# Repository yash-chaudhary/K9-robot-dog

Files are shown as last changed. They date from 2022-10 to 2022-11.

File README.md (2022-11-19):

# K9 Robot Dog

The COVID-19 pandemic gripped the world with its harsh lockdowns, lonely isolation, and imaginary
human contact. It turned loving families into raging chihuahua’s. But it was our pets that continued to
love us unconditionally. This report will demonstrate the development of K9 - man’s best robot friend

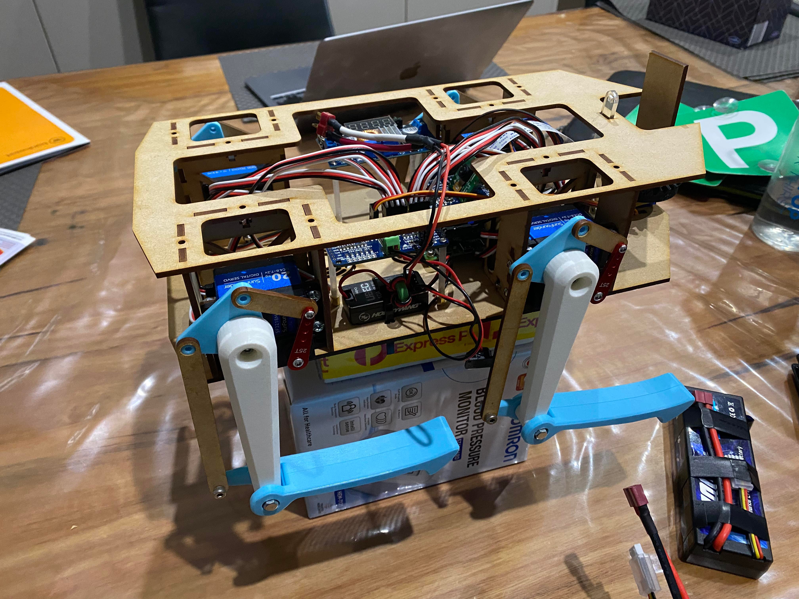
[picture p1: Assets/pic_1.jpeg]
Image of Physical Robot 1

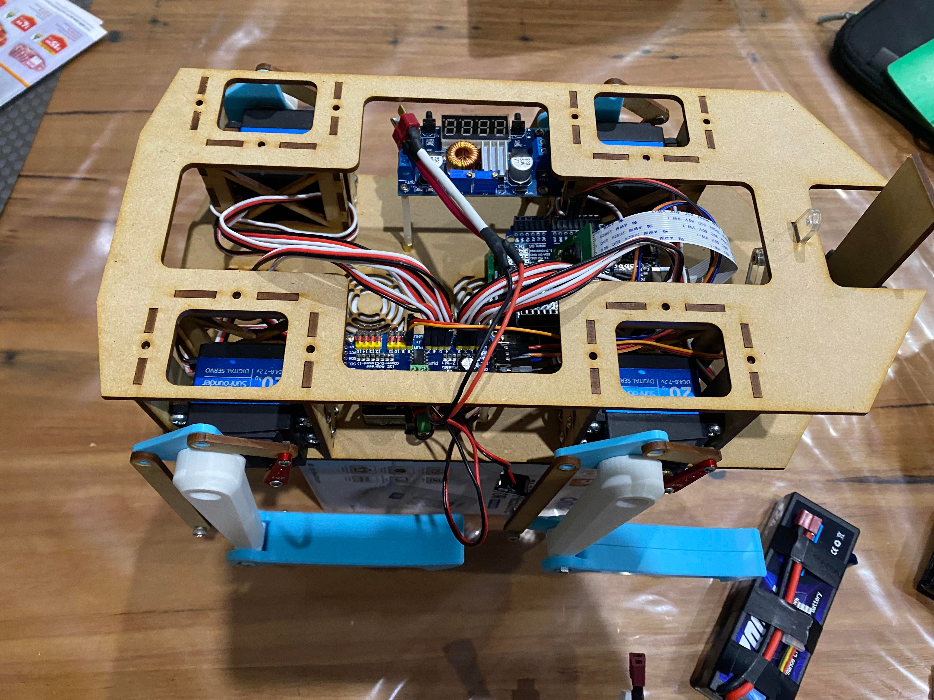
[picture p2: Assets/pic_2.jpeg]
Image of Physical Robot 2


### Software Design

Python was used to program a Raspberry Pi 4 Model B to leverage the open source real-time computer vision library, openCV. Using a
camera module, this python library is able to define the landmarks on a hand(s) to figure out how many figures a person is holding up
in real-time. Once it is able to recognise the gesture it sends this number as a command via the UART communication protocol to an
Arduino Uno which reads the command and executes the routine corresponding to the command. The Arduino Uno is a microcontroller as opposed
to a microprocesser which allows to it control it's I/O peripherals quite quickly which is incredibly important for the controlled motion
of quadrupedal motion.

As an aside, a couple of hours before the reveal of the robot, the gesture recogition software had an undetected bug. To restore
motion to the robot, an ultrasonic sensor was used, where instead of using a camera module with gesture recognition the ultrasonic sensor would detect the distance between itself and an obstacle in its field of view. Different distance thresholds away from the ultrasonic sensor were defined to control the movement of the robot with a 1 second delay between each command.

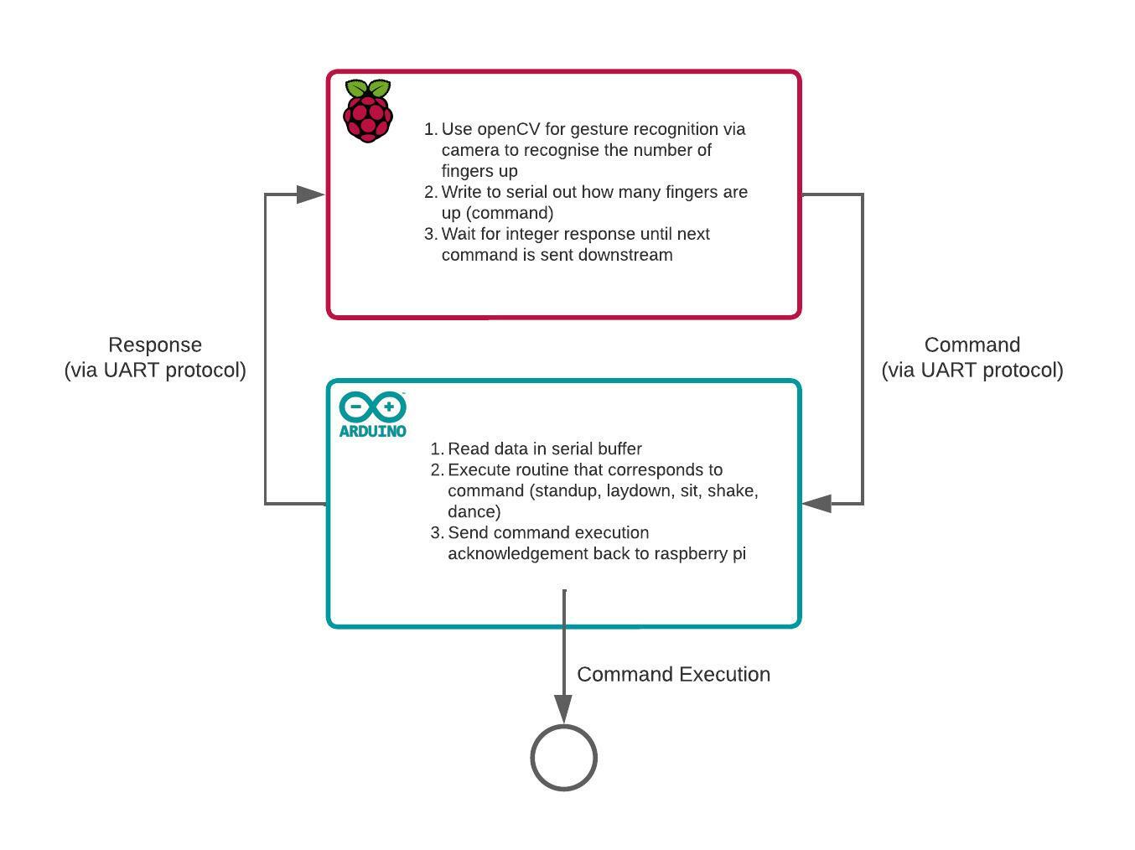
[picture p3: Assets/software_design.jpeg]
Image of Software Design


### Electrical Design

The first electronics track is the power transmission used to command the servo motors and it involves a 7.4V two-cell lithium polymer battery connected to a DPDT switch. The switch controls the power supply to a buck converter (DC-DC converter) that drops the 7.4V from the LiPo batteries to a 5V supply. The output from the buck converter is a regulated 5V supply from a USB-A connector that is connected to a Raspberry Pi Model 4 B via USB-C. The USB-A port from the Raspberry Pi is then connected to the serial port of the Arduino. Then using the 5V output pin on the Arduino, the PCA9685 Servo Driver is powered by connecting the 5V output to the PCA9685 VCC pin. This VCC pin is strictly used to power the PCA9685 chip. Other pins are required to ensure the servo driver works. The ground pin of the servo driver is connected to the ground pin on the Arduino and the SDA (serial data) and SCL (serial clock) are connected to the SDA and SCL pins on newer Arduinos or analogue pin 4 and 5 respectively on older Arduinos. These two pins allow the Arduino and PCA9685 to communicate to each other via the I2C communication protocol. This completes the power supply to the Raspberry Pi, Arduino and PCA9685 that are used to command the servo motors. The second electronics track is used to power the servo motors. Again a 7.4V two cell lithium polymer battery is used and it is connected to a universal battery eliminator circuit (essentially another buck converter) that steps down the battery supply voltage from 7.4V to 6V at a maximum supply current of 10A. The output of the universal battery eliminator circuit is connected to the terminal block on the PCA9685, and it also has a SPST switch to control the power supply. Each of the 3-pin servo motors that need to be controlled are connected to the PCA9685 where the top pin is the PWM signal pin, the middle pin is the V+ supply coming from the external battery power supply, and the last pin being ground. The completes the circuit to supply power to all the servos.

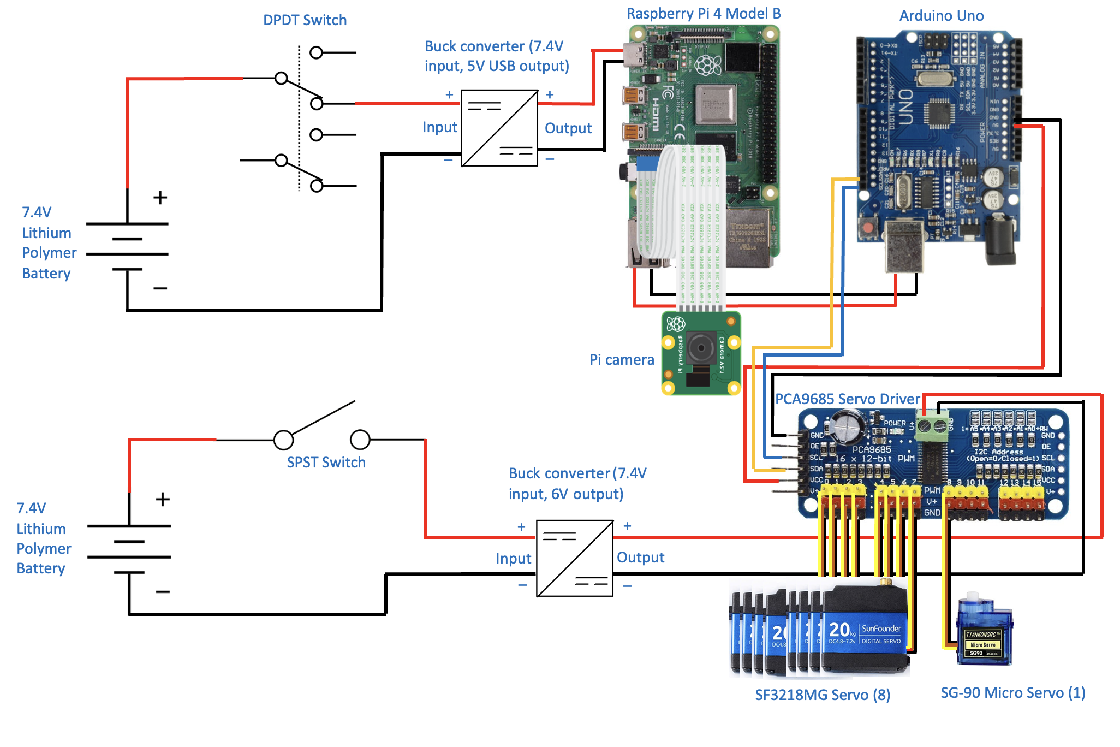
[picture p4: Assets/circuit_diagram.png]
Image of Electrical Design


### Mechanical Design

Calculations were conducted find out the max loading the servo motors would withstand. After this, the parts were designed in
Solidworks with load bearing components undergoing Finite Element Analysis (FEA) to ensure they don't fail under load. These components
were the ones that were going to be 3D printed. The rest of the components were laser cut with MDF and acrylic. One of the highlights
for the design was the use of captive nut and bolt t-solts that removed the need for any permanent joints in the design. Another insight was
that traditional robot dog designs have the mass of the servo motors controlling the lower leg was overhanging from the chassis, this design can lead to instabilities due to the potential for moments to occur which can topple the robot in the roll axis. So the goal was
to find a different design that kept the distribution of mass closer to the centre of mass to increase stability and handling of the robot during movements. A servo configuration that retained both the servos within the chassis with no large mass overhangs was found. The result is that stability was increased relative to other quadruped designs as the mass is concentrated closer to the centre of mass instead of hanging off the outer parts of the legs which can cause unwanted moments when moving the robot. Also the robot deliberating had a wider
body to further increase stability

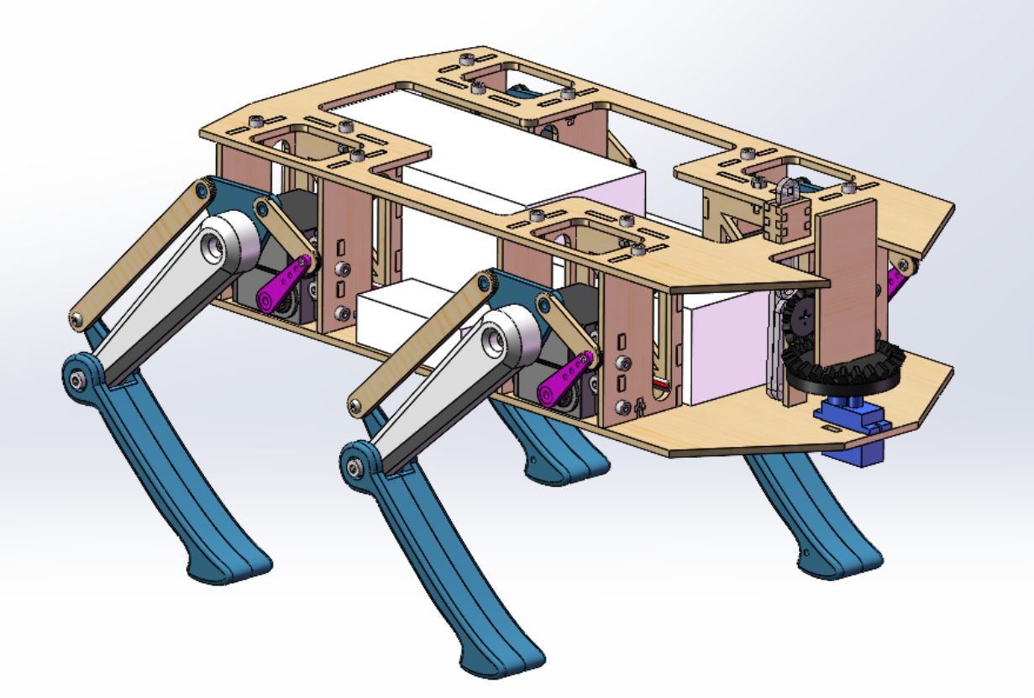
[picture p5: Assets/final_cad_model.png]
Image of CAD design

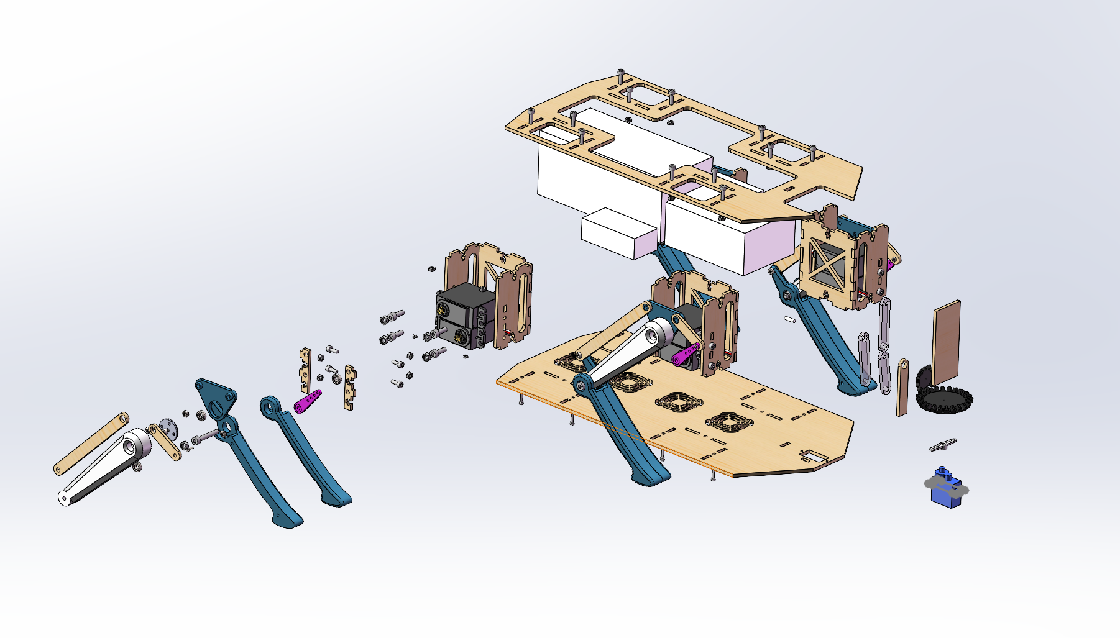
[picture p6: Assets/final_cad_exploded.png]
Image of CAD exploded view


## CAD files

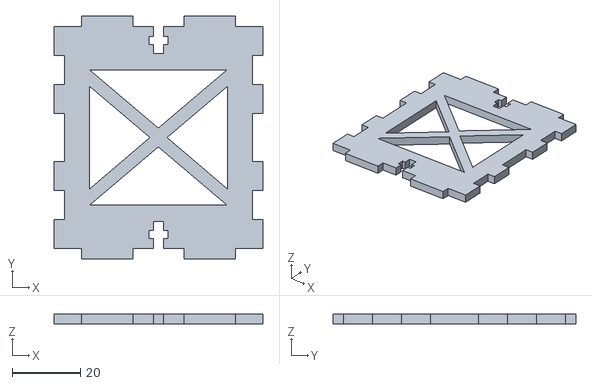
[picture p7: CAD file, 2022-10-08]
CAD/Chassis parts/Motor Back Plate (L 55mm W 65 mm D 3mm).stl
61.0 x 71.0 x 3.00

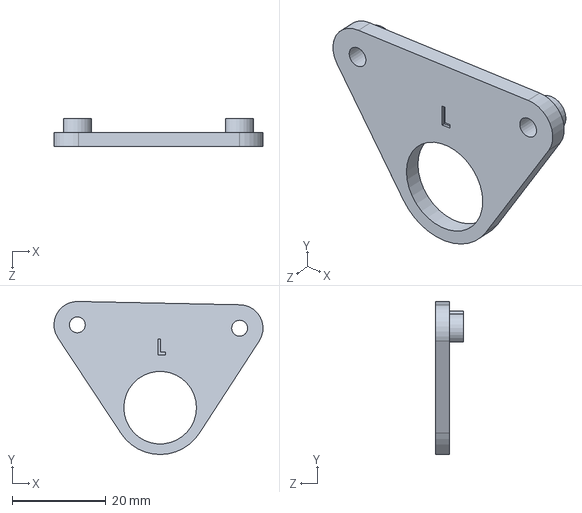
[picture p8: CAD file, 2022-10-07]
CAD/Leg parts/production_parts/15-5mm_left_linkage_plate.SLDPRT
44.6 x 32.7 x 6.00 mm

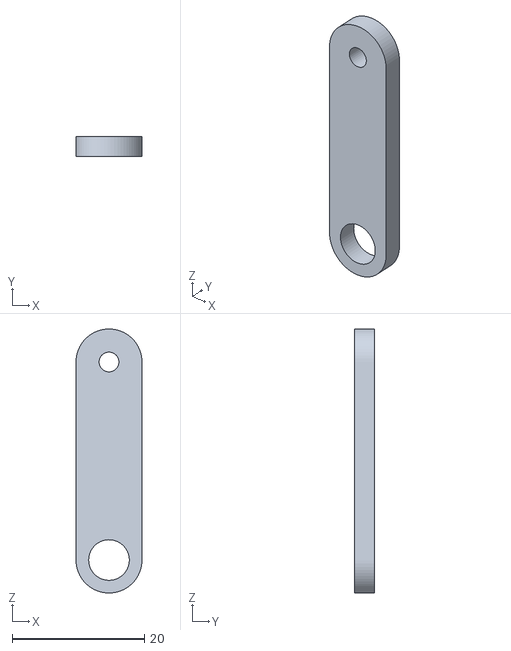
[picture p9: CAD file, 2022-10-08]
CAD/Leg parts/production_parts/linkages/V4_30mm_solid_arm v2.stl
10.0 x 3.00 x 40.0

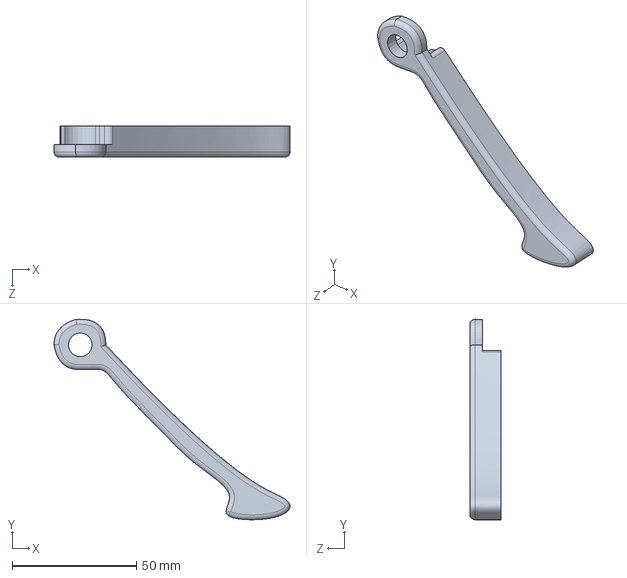
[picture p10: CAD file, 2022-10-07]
CAD/Leg parts/production_parts/lower_leg_v2/100mm_OUTER_RIGHT_lower_leg_v2.SLDPRT
95.0 x 80.7 x 12.5 mm

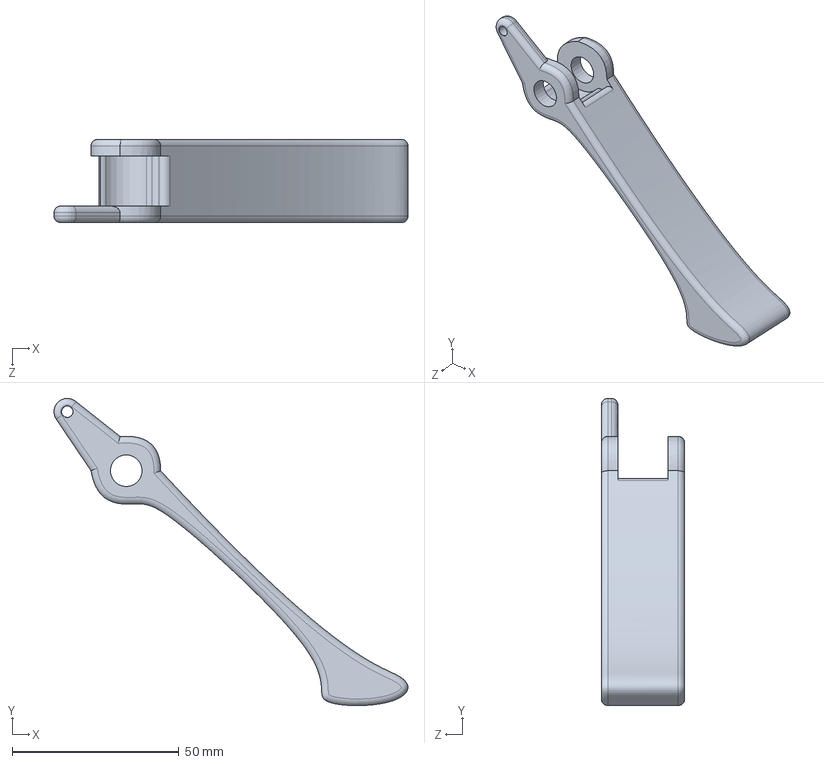
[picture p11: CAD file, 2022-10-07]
CAD/Leg parts/protoyped_parts/lower_leg/100mm_left_lower_leg_clean.SLDPRT
106.1 x 92.1 x 25.0 mm

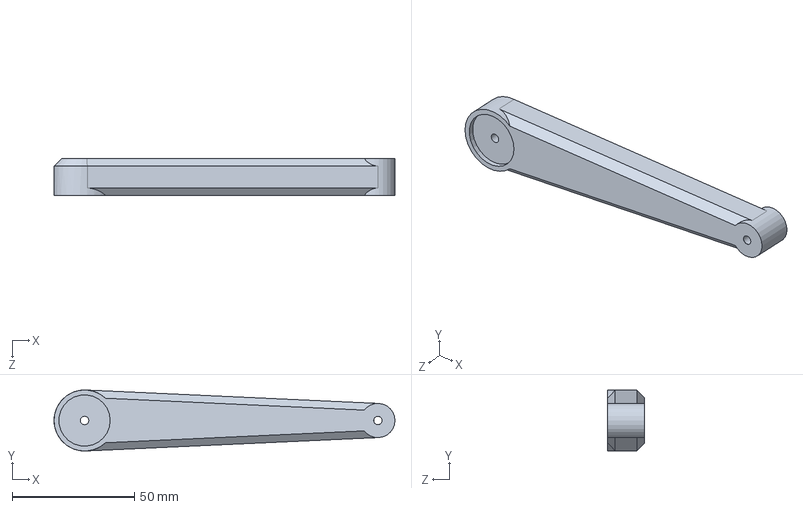
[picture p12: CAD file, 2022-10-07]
CAD/Leg parts/protoyped_parts/upper_leg/upper_leg_solid.SLDPRT
139.5 x 24.9 x 15.0 mm

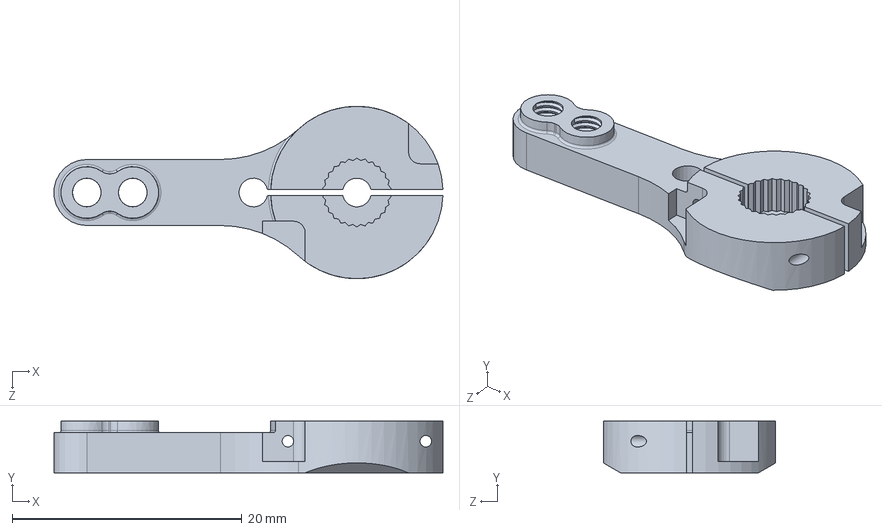
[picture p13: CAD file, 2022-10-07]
CAD/Servo arm parts/servo_arm_25T.SLDPRT
33.8 x 4.50 x 15.0 mm

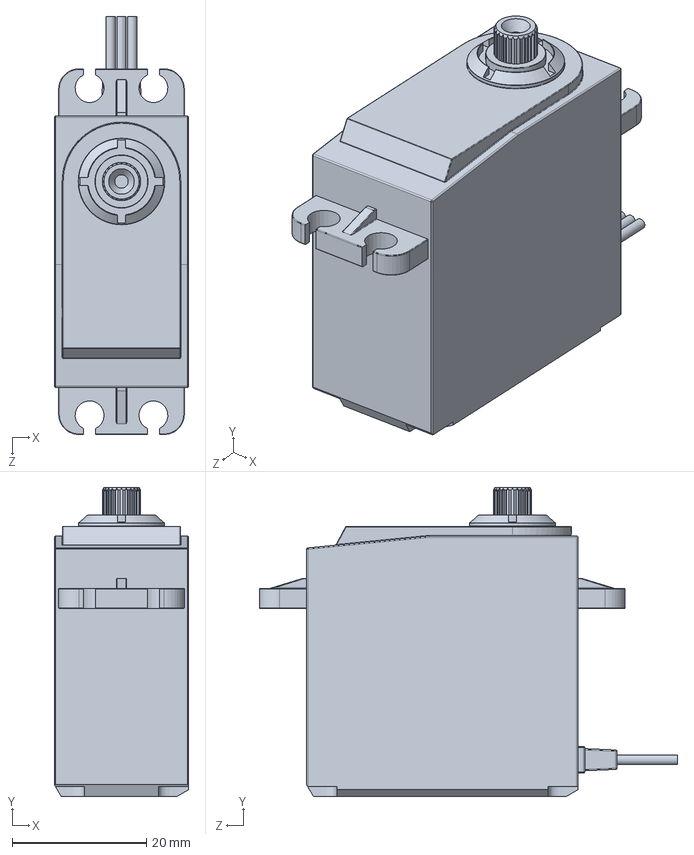
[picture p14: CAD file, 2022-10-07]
CAD/Servo motor parts/SunFounder_20kg_Servo_Motor.SLDPRT
20.0 x 46.0 x 62.2 mm

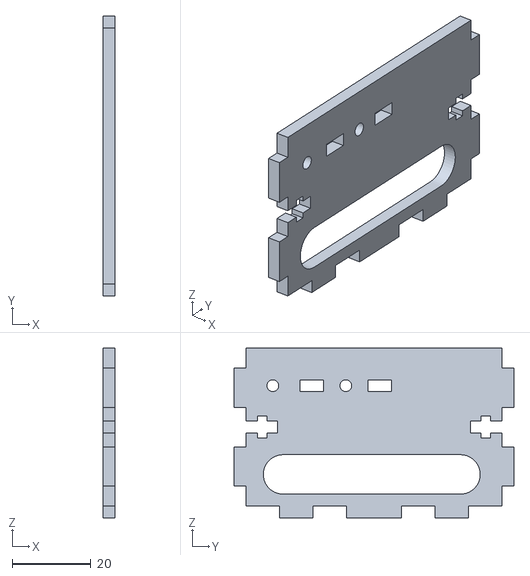
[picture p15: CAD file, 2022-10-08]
CAD/Chassis parts/Motor Side Plate (L 40mm W 40mm D 3mm).stl
3.00 x 71.0 x 43.0

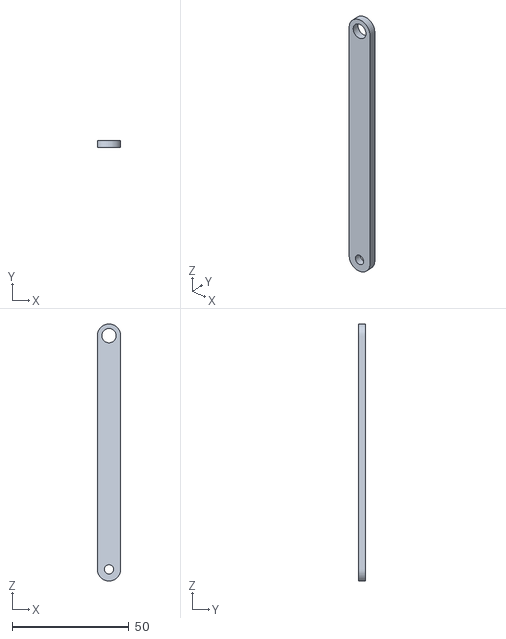
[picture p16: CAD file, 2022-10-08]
CAD/Leg parts/production_parts/linkages/V4_100mm_solid_arm v2.stl
10.0 x 3.00 x 110.0

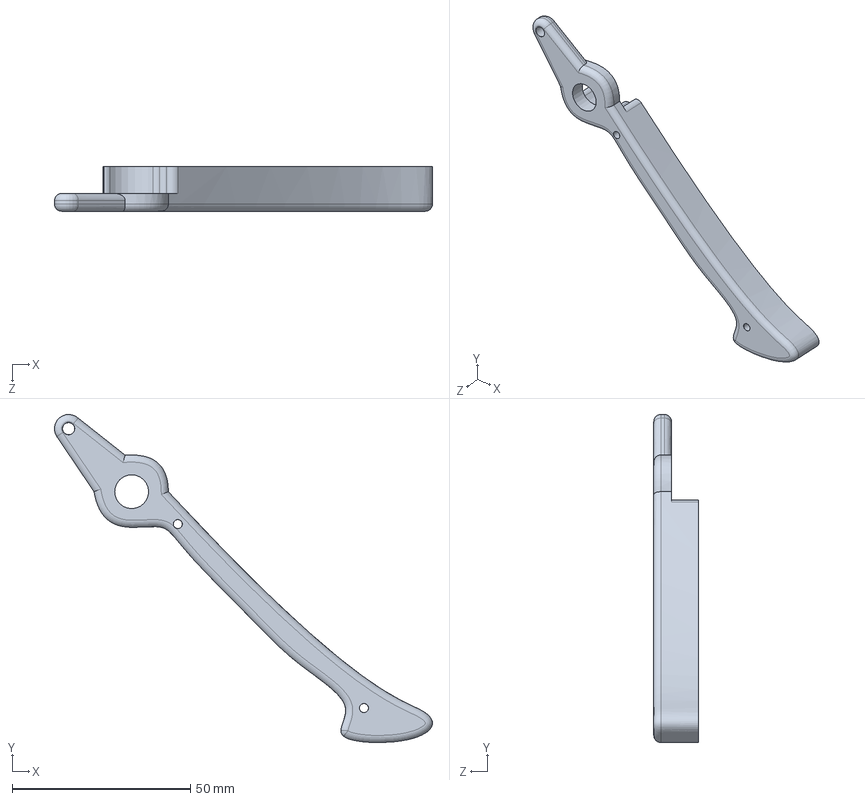
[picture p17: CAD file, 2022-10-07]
CAD/Leg parts/production_parts/lower_leg_v2/100mm_INNER_LEFT_lower_leg_v2.SLDPRT
106.1 x 92.1 x 12.5 mm

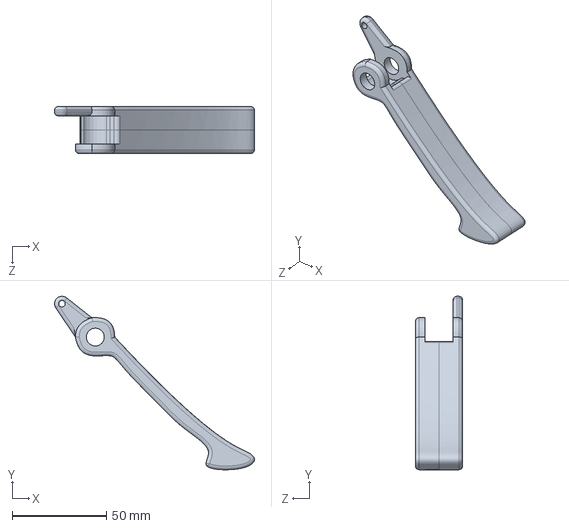
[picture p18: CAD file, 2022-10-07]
CAD/Leg parts/protoyped_parts/lower_leg/100mm_right_lower_leg_v2.SLDPRT
106.1 x 92.1 x 25.0 mm

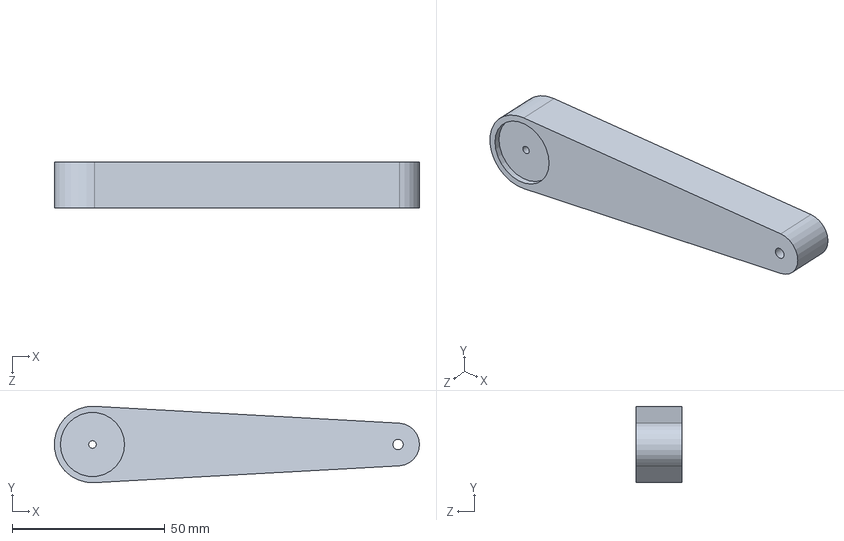
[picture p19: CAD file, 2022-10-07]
CAD/Leg parts/protoyped_parts/upper_leg/upper_leg_test.SLDPRT
119.4 x 25.0 x 15.0 mm

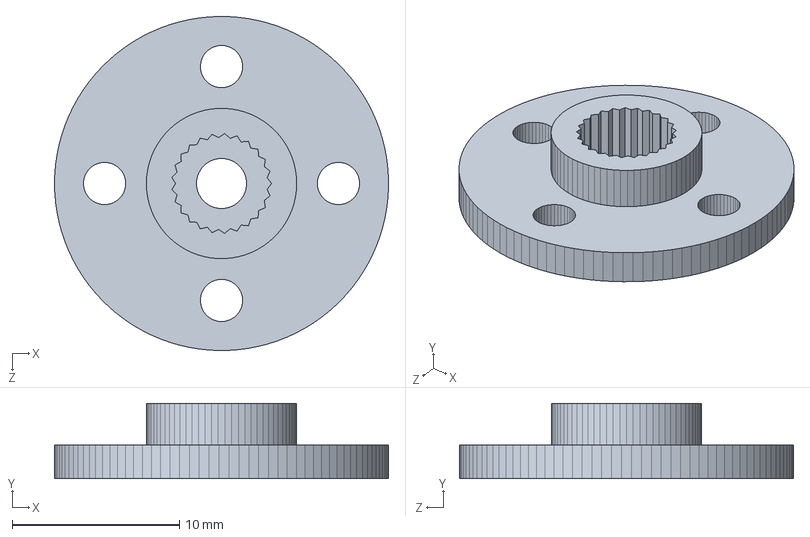
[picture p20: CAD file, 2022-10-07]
CAD/Servo arm parts/servo_horn_25T.SLDPRT
20.0 x 4.50 x 20.0 mm

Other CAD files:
CAD/Leg parts/production_parts/15-5mm_right_linkage_plate.SLDPRT
CAD/Chassis parts/Motor Bracket (L 40mm W 7mm D 3mm).stl
CAD/Leg parts/production_parts/100mm_upper_leg_solid.SLDPRT
CAD/Leg parts/production_parts/lower_leg_v2/100mm_OUTER_LEFT_lower_leg_v2.SLDPRT
CAD/Leg parts/production_parts/100mm_upper_leg_solid.STL
CAD/Leg parts/production_parts/15-5mm_left_linkage_plate.STL
CAD/Leg parts/production_parts/15-5mm_right_linkage_plate.STL
CAD/Leg parts/production_parts/lower_leg_v1/100mm_LEFT_INNER_lower_leg_solid.SLDPRT
CAD/Leg parts/production_parts/lower_leg_v1/100mm_LEFT_INNER_lower_leg_solid.STL
CAD/Leg parts/production_parts/lower_leg_v1/100mm_LEFT_OUTER_lower_leg_solid.SLDPRT
CAD/Leg parts/production_parts/lower_leg_v1/100mm_LEFT_OUTER_lower_leg_solid.STL
CAD/Leg parts/production_parts/lower_leg_v1/100mm_RIGHT_INNER_lower_leg_solid.SLDPRT
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

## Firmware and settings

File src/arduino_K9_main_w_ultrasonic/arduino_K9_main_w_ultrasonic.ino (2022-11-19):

/*  
 *  Project Name: K9
 *  Author: Yash Chaudhary
 *  Date Created: 04/10/2022
 *    
 *    ------ PRELIMINARY NOTES ------ 
 *  Servo motors SF3218MG can move from 0 to 270 degrees and are mounted on chassis sideways.
 *  Before mounting upper and lower leg assembly run the motor calibration code that will set the motors to the neutral position at 135 degrees.
 *  The servo neutral position can be moved to 135 degrees giving the robot +/- 135 degrees of motion at the joints. 
 *  The kinematic model chosen for this project is forward kinematics where the angles of the joints are specified to move the robot to its desired configuration
 *  This is a brute force method used to actuate the robot by essentially finding the angles of movement via trial and error
 *  
 *  NOTE that the head will move only for certain commands and operates betweeo 0 and 180 degrees where 90 degrees is its neutral position
 *  
 *  Using ultrasonic sensor to control motion
 *  
 */

#include <Wire.h>                       // library for I2C communication
#include <Adafruit_PWMServoDriver.h>    // library for PCA9685 servo driver 

// create instance of Adafruit_PWMServoDriver class with default address 0x40
Adafruit_PWMServoDriver pwm = Adafruit_PWMServoDriver(0x40, Wire);

// servo constants
#define SERVOMIN  85          // minimum servo pulse length count (out of 4096)
#define SERVOMAX  460         // maximum servo pulse length count (out of 4096)
#define USMIN  500            // rounded minimum microsecond length based on the minimum pulse of 80
#define USMAX  2500           // rounded maximum microsecond length based on the maximum pulse of 470
#define SERVO_FREQ 50         // analog servo frequency at 50Hz or pulse every 20ms
#define SERVO_COUNT 8         // number of servo actuators (8 leg servos + 1 head servo)

// ultrasonic initialisations
const int echo_pin = 2;
const int trigger_pin = 3;
int distance_cm;
long duration_us;
const int LAYDOWN_THRES = 5;
const int STANDUP_THRES = 10;
const int SIT_THRES = 15;
const int SHAKE_THRES = 20;
const int DANCE_THRES = 25;

/*
 * updated_servo_angle[0] assigned to front right upper leg
 * updated_servo_angle[1] assigned to front right lower leg
 * updated_servo_angle[2] assigned to front left upper leg
 * updated_servo_angle[3] assigned to front left lower leg
 * updated_servo_angle[4] assigned to back right upper leg
 * updated_servo_angle[5] assigned to back right lower leg
 * updated_servo_angle[6] assigned to back left upper leg
 * updated_servo_angle[7] assigned to back left upper leg
 * updated_servo_angle[8] assigned to head 
 */
const int init_leg_servo_angle = 135;    // initial leg servo positions
int updated_servo_angle[8];              // updated servo positions

// function prototypes
void set_servo_position();
int map_angle(int angle, int max_deg);
void standup();
void laydown();
void sit();
void shake();
void dance();
void walk();


// ------------------------------------------------------------------- SETUP -------------------------------------------------------------------

void setup() {

  // pins for ultrasonic sensor
  pinMode(trigger_pin, OUTPUT);             // Sets the trig_pin as an OUTPUT
  pinMode(echo_pin, INPUT);                 // Sets the echo_pin as an INPUT
  
  Serial.begin(9600);                       // establishing serial connection at baud rate of 9600 bits/s
  
  pwm.begin();                              // being pwm object
  pwm.setOscillatorFrequency(27000000);     // set IC oscillator frequency to get expected pmw update frequency 
  pwm.setPWMFreq(SERVO_FREQ);               // set pwm frequency based on servo operating frequency

}

// ------------------------------------------------------------------- LOOP -------------------------------------------------------------------

void loop() {

  // get distance from ultrasonic sensor
  digitalWrite(trigger_pin, LOW);                  // initially setting trig_pin LOW to get a clean HIGH pulse
  delayMicroseconds(5);
  digitalWrite(trigger_pin, HIGH);
  delayMicroseconds(10);                        // use trigger pin to generate pulse 
  digitalWrite(trigger_pin, LOW);

 
  duration_us = pulseIn(echo_pin, HIGH);        // measure duration of pulse from echo pin

  distance_cm = 0.017 * duration_us;            // calculate distance to bounding object

  Serial.print("Distance: ");
  Serial.print(distance_cm);
  Serial.println(" cm\n");

  // command K9 based on distance to bounding object (hand)
  if(distance_cm <= LAYDOWN_THRES) {
    laydown();
    Serial.println("Laydown command EXECUTED");
    delay(1000);
  }

  else if((distance_cm > LAYDOWN_THRES) && (distance_cm <= STANDUP_THRES)) {
    standup();
    Serial.println("Standup command EXECUTED");
    delay(1000);
  }

  else if((distance_cm > STANDUP_THRES) && (distance_cm <= SIT_THRES)) {
    sit();
    Serial.println("Sit command EXECUTED");
    delay(1000);
  }

  else if((distance_cm > SIT_THRES) && (distance_cm <= SHAKE_THRES)) {
    shake();
    Serial.println("Shake command EXECUTED");
    delay(1000);
  }

  else if(distance_cm > SHAKE_THRES && (distance_cm <= DANCE_THRES)) {
    dance();
    Serial.println("Dance command EXECUTED");
    delay(1000);
  }

  delay(1000);
  
}

// ------------------------------------------------------------------- MOTOR CONTROL -------------------------------------------------------------------

// function that moves servos to correct positions 
void set_servo_position() {

  int pulse_len;
  
  // iterate through updated angle for each servo
  for(int servo_num = 0; servo_num < SERVO_COUNT; servo_num++) {          
    
    // controls movement of leg servos
    pulse_len = map_angle(updated_servo_angle[servo_num], 270);           // map updated servo angle position to assocaited pulse length value
    pwm.setPWM(servo_num, 0, pulse_len);                                  // move servo to specified position 
  }  
}

// function to map angle to pulse length 
int map_angle(int angle, int max_deg) {
  int pulse_length_angle = map(angle, 0, 270, SERVOMIN, SERVOMAX);        // mapping with min, max servo pulse length
  return pulse_length_angle; 
 
}


// ---------------------------------------------------------------------- ROUTINES ---------------------------------------------------------------------- 

// standup routine 
void standup() {

  // can add a delay to maybe standup back legs before front legs 
  updated_servo_angle[0] = init_leg_servo_angle - 55;       // front right upper leg 
  updated_servo_angle[1] = init_leg_servo_angle - 25;       // front right lower leg
  
  updated_servo_angle[2] = init_leg_servo_angle + 40;       // front left upper leg
  updated_servo_angle[3] = init_leg_servo_angle + 30;       // front left lower leg
  
  updated_servo_angle[4] = init_leg_servo_angle - 55;       // back right upper leg
  updated_servo_angle[5] = init_leg_servo_angle - 25;       // back right lower leg
  
  updated_servo_angle[6] = init_leg_servo_angle + 40;       // back left upper leg
  updated_servo_angle[7] = init_leg_servo_angle + 30;       // back left lower leg

  set_servo_position();
}


// laydown routune 
void laydown() {
  
   updated_servo_angle[0] = init_leg_servo_angle;      // front right upper leg (FRU)
   updated_servo_angle[1] = init_leg_servo_angle;      // front right lower leg (FRL)
   
   updated_servo_angle[2] = init_leg_servo_angle;      // front left upper leg  (FLU)
   updated_servo_angle[3] = init_leg_servo_angle;      // front left lower leg   (FLL)
   
   updated_servo_angle[4] = init_leg_servo_angle;      // back right upper leg (BRU)
   updated_servo_angle[5] = init_leg_servo_angle;      // back right lower leg (BRL)
   
   updated_servo_angle[6] = init_leg_servo_angle;      // back left upper leg (BLU)
   updated_servo_angle[7] = init_leg_servo_angle;      // back left lower leg (BLL)

   set_servo_position();
}


// sit routine 
void sit() {

   updated_servo_angle[0] = init_leg_servo_angle - 45;       // front right upper leg 
   updated_servo_angle[1] = init_leg_servo_angle - 45;       // front right lower leg
  
   updated_servo_angle[2] = init_leg_servo_angle + 45;       // front left upper leg
   updated_servo_angle[3] = init_leg_servo_angle + 45;       // front left lower leg
   
   updated_servo_angle[4] = init_leg_servo_angle - 10;       // back right upper leg
   updated_servo_angle[5] = init_leg_servo_angle - 10;       // back right lower leg 
   
   updated_servo_angle[6] = init_leg_servo_angle + 10;       // back left upper leg
   updated_servo_angle[7] = init_leg_servo_angle + 10;       // back left lower leg 

   set_servo_position(); 
  
}


// shake routine
void shake() {

   updated_servo_angle[0] = init_leg_servo_angle + 20;       // front right upper leg 
   updated_servo_angle[1] = init_leg_servo_angle;            // front right lower leg
  
   updated_servo_angle[2] = init_leg_servo_angle + 45;       // front left upper leg
   updated_servo_angle[3] = init_leg_servo_angle + 45;       // front left lower leg
   
   updated_servo_angle[4] = init_leg_servo_angle - 10;       // back right upper leg
   updated_servo_angle[5] = init_leg_servo_angle - 10;       // back right lower leg 
   
   updated_servo_angle[6] = init_leg_servo_angle + 10;       // back left upper leg 
   updated_servo_angle[7] = init_leg_servo_angle + 10;       // back left lower leg

   set_servo_position(); 
}

// dance routine
void dance() {

  standup();          // must start in standup stance

  delay(1000);        // delay to allow servos to move to standup stance

  int moves_to_bust = 4;   // number of moves to be made

  // loop to make dance move
  for(int i = 0; i < moves_to_bust; i++) {
  
  // servo positions for moving up
  updated_servo_angle[0] = init_leg_servo_angle - 20;       // front right upper leg 
  updated_servo_angle[1] = init_leg_servo_angle - 40;       // front right lower leg
  
  updated_servo_angle[2] = init_leg_servo_angle + 15;       // front left upper leg
  updated_servo_angle[3] = init_leg_servo_angle + 45;       // front left lower leg

  updated_servo_angle[4] = init_leg_servo_angle - 20;       // back right upper leg
  updated_servo_angle[5] = init_leg_servo_angle - 50;       // back right lower leg
  
  updated_servo_angle[6] = init_leg_servo_angle + 15;       // back left upper leg
  updated_servo_angle[7] = init_leg_servo_angle + 45;       // back left lower leg

  set_servo_position();

  delay(1000);  // delay before changing back to standup stance

   // go back down to standing stance
  standup();

  }
   
  
}


// ------------------------------------------------------------------------------------------------------------------------------------------------------ 

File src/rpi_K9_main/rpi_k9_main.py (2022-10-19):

'''
    The following code is used to send gesture commands a rpi and pi camera to an
    Arduino to control servo movements of the robot dog K9. 
'''

import serial  # module required for serial communication
import time    # module required to use delays

# imports for gesture recognition using a pi camera
import cv2
from collections import Counter
from module import findnameoflandmark,findpostion
import math

# constants
PORT = '/dev/ttyUSB0'    # serial port that Arduino is connected to
BAUD_RATE = 9600         # bits per second data transfer


on_count = 0

# --------------------------------------------------------- DRIVING CODE ---------------------------------------------------------

if __name__ == '__main__':
    ser = serial.Serial(PORT, BAUD_RATE, timeout = 1)    # initialise ser object
    ser.flush()                                          # remove any old data that was still in buffer
    
    
    # use CV2 Functionality to create a Video stream and add some values + variables
    cap = cv2.VideoCapture(0)
    tip=[8,12,16,20]
    tipname=[8,12,16,20]
    fingers=[]
    finger=[]

    # loop for continual serial communication
    while True:
        
        # --------------------------------------- CAMERA CODE --------------------------------------------
        ret, frame = cap.read() 
      
     
        # determines the frame size, 640 x 480 offers a nice balance between speed and accurate identification
        frame1 = cv2.resize(frame, (640, 480))
    
        # determine location of the joints of the fingers 
        a=findpostion(frame1)
        b=findnameoflandmark(frame1)
     
        #determine if a finger is up or down and
        if len(b and a)!=0:
            finger=[]
            if a[0][1:] < a[4][1:]: 
                finger.append(1)
                print (b[4])
          
            else:
                finger.append(0)   
        
            fingers=[] 
            for id in range(0,4):
                if a[tip[id]][2:] < a[tip[id]-2][2:]:
                    print(b[tipname[id]])

                    fingers.append(1)
    
                else:
                    fingers.append(0)
                          
        x=fingers + finger
        c=Counter(x)
        up=c[1]
        down=c[0]
        print('This many fingers are up - ', up)

        
        # -----------------------------------------------------------------------------------------------
        command = ""
        if(up == 1):
            command = "laydown\n"
        elif(up == 2):
            command = "standup\n"
        elif (up == 3):
            command = "sit\n"
        elif (up == 4):
            command = "shake\n"
        elif (up == 5):
            command = "dance\n"
        else:
            command = "standup\n"
            
        if(on_count == 0):
            time.sleep(5)
            on_count += 1
        else:
            time.sleep(1)
        
        ser.write(command.encode('utf-8'))
        status = int(ser.readline().decode('utf-8').rstrip())   # integer 1 is returned
        if (status == 1):
            print("Arduino LED turned " + command)
        else:
            print("command FAILED")
  
    


            
            

        
                
           
            
            
        

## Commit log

2022-09-23 create servo tests
2022-10-04 add motor code
2022-10-04 update motor calibration
2022-10-05 change motor control to use pulse length instead of microseconds
2022-10-05 update motor calibration comments
2022-10-05 fix issues with forward kinematics
    [forward_kinematics_K9_motor_control.ino, motor_calibration.ino]
2022-10-07 add CAD files
    [100_right_lower_leg_v2.SLDPRT, 100mm_INNER_LEFT_lower_leg_v2.SLDPRT, 100mm_INNER_LEFT_lower_leg_v2.STL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]
2022-10-08 update CAD STL files
    [Motor Back Plate (L 55mm W 65 mm D 3mm).stl, Motor Bracket (L 40mm W 7mm D 3mm).stl, Motor Side Plate (L 40mm W 40mm D 3mm).stl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]
2022-10-08 update forward kinematics
2022-10-12 update forward kinematic
